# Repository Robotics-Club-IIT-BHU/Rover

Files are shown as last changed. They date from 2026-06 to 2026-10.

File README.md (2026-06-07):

# Rover
## Drive:
Clone the src file and build the package
then run using : ros2 launch drive sim.launch.py

## RtabMap:
Build RTABMAP ROS: https://github.com/introlab/rtabmap_ros
and run in second terminal using : ros2 launch rtabmap_launch rtabmap.launch.py    rgb_topic:=/camera/color/image_raw    depth_topic:=/camera/depth/image_raw    camera_info_topic:=/camera/camera_info    frame_id:=base_link    odom_topic:=/odom    approx_sync:=true

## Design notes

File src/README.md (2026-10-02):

# Athena

Athena is a six-wheeled outdoor rover (ROS 2 Humble, NVIDIA Jetson). Give it a
GPS coordinate, or click a point, and it drives there, steering around
obstacles it sees. A Pixhawk supplies IMU and GPS, a RealSense D435i supplies
obstacles and visual odometry, and a Raspberry Pi Pico drives the six motors.

This page is **how to run it**. How it is built: [docs/ARCHITECTURE.md](docs/ARCHITECTURE.md).

| I want to | Read |
|---|---|
| Understand the packages, data flow, frames, design decisions | [docs/ARCHITECTURE.md](docs/ARCHITECTURE.md) |
| Run, tune, test or fix navigation | [athena_gps_nav/README.md](athena_gps_nav/README.md) |
| Wire (pin map), calibrate, flash or debug the motors | [athena_drive/README.md](athena_drive/README.md) |
| SSH in, get through WiFi login, use `rviz2` from a laptop | [athena_remote/README.md](athena_remote/README.md) |
| Every Foxglove panel, goal, waypoint and troubleshooting step | [athena_remote/docs/FOXGLOVE_PANEL.md](athena_remote/docs/FOXGLOVE_PANEL.md) |
| Test navigation from the Foxglove panel | [athena_remote/TESTING.md](athena_remote/TESTING.md) |
| Change code, build, use git | [CONTRIBUTING.md](CONTRIBUTING.md) |

## Contents

1. [Get a shell on the rover](#1-get-a-shell-on-the-rover)
   - [Log in to the institute WiFi](#log-in-to-the-institute-wifi)
2. [Bring the rover up](#2-bring-the-rover-up)
3. [Check it is healthy](#3-check-it-is-healthy)
4. [Connect Foxglove (the control panel)](#4-connect-foxglove-the-control-panel)
5. [Send it somewhere](#5-send-it-somewhere)
6. [Everyday commands](#6-everyday-commands)
7. [Hardware](#7-hardware)
8. [Current state](#8-current-state-hardware-last-verified-september-2026)

---

## 1. Get a shell on the rover

Everything below is typed on the Jetson, over SSH:

```bash
ssh robo@172.20.119.87
```

`172.20.119.87` is the address on 2026-10-02. It changes with DHCP: on the
Jetson, `hostname -I` prints it; from another machine on the same WiFi,
`ssh robo@ubuntu.local` usually works. Finding it by scanning, and a host alias
that also opens the Foxglove tunnel:
[athena_remote](athena_remote/README.md#getting-a-shell-on-the-jetson).

`~/.bashrc` on the Jetson sources ROS and the workspace and sets
`ROS_DOMAIN_ID=42`. A shell that skips it (`ssh host 'command'`, cron) is on
domain 0 and sees an empty graph:
[fix](athena_remote/README.md#getting-a-shell-on-the-jetson).

### Log in to the institute WiFi

The institute WiFi puts a login page in front of the internet, and the Jetson has
no screen to show it on. Log it in from your SSH session instead. The login page
blocks only the internet, so you can still SSH to the Jetson from a laptop on the
same WiFi before it is logged in.

**1. Is a login needed?**

```bash
curl -s -o /dev/null -w "%{http_code}\n" http://connectivitycheck.gstatic.com/generate_204
```

`204` means it is already online and there is nothing to do. Anything else means
the login page is intercepting it.

**2. Log in by hand (first time, or when the automatic login fails).** `w3m` is a
text web browser, already installed on the Jetson:

```bash
w3m http://connectivitycheck.gstatic.com/generate_204
```

The login page opens in the terminal. Fill it in like a normal page:

| Key | Does |
|---|---|
| `Tab` / arrow keys | move between fields and buttons |
| `Enter` on a field | start typing; `Enter` again to accept |
| `Enter` on the login button | submit |
| `q`, then `y` | quit |

Run the `curl` from step 1 again: `204` means you are through.

**3. Let it log itself in (optional).** `captive_login` reads the login form once,
then logs in with your saved username and password:

```bash
ros2 run athena_remote captive_login --ros-args -p mode:=discover   # ONE TIME: writes ~/.config/athena_remote/portal.yaml
vim ~/.config/athena_remote/portal.yaml                             # fill in your username and password (i to type, Esc then :wq to save)
ros2 run athena_remote captive_login                                # log in (does nothing if already online)
```

Your password stays in `~/.config/athena_remote/portal.yaml` on the Jetson: it is
not in the repo, the file is readable only by you, and it is never logged.

**4. Stay logged in (optional).** Run `crontab -e` and add these two lines. The
first logs in at boot; the second re-logs in every 10 minutes if the session
expired:

```
@reboot      sleep 30 && . /opt/ros/humble/setup.sh && ~/athena/install/athena_remote/lib/athena_remote/captive_login
*/10 * * * * . /opt/ros/humble/setup.sh && ~/athena/install/athena_remote/lib/athena_remote/captive_login
```

Keep the `. /opt/ros/humble/setup.sh` part: without it the cron job fails
silently. Logged in but still no internet (`apt`, `git` fail): check
[the clock](#correcting-the-clock). If the automatic login fails (JavaScript login
pages, changing tokens):
[CAPTIVE_PORTAL.md](athena_remote/docs/CAPTIVE_PORTAL.md).

## 2. Bring the rover up

```bash
ros2 launch athena_gps_nav bringup.launch.py
```

One command starts the entire stack, staggered so each layer has what it
depends on before it starts. Give it about 40 seconds to settle.

| Elapsed | Starts | Why it waits |
|---|---|---|
| 0 s | RealSense camera, Pixhawk bridge, robot description | nothing works without sensor data |
| 0 s | Motor bridge | not delayed: it opens the Pico serial link, then waits for a `/cmd_vel` that only arrives once Nav2 is up |
| 5 s | Visual odometry (rtabmap) | needs camera images already flowing |
| 8 s | Both EKFs and the GPS transform | need odometry and IMU to fuse |
| 12 s | Nav2: planner, controller, costmaps | needs a position estimate before it can plan |
| 15 s | Foxglove bridge and the panel's nodes | only useful once there is data to show |

### Launch options

`bringup.launch.py` takes exactly these four arguments. Anything else is
silently accepted by `ros2 launch` and then ignored, so a typo costs you a run
(`--show-args` lists the real ones).

```bash
# motors receive no commands (logged, not sent); safe with the rover on a bench
ros2 launch athena_gps_nav bringup.launch.py dry_run:=true

# no RealSense: no obstacle avoidance AND no visual odometry, so the EKFs
# dead-reckon on the Pixhawk alone
ros2 launch athena_gps_nav bringup.launch.py use_camera:=false

# no control panel: lower CPU load
ros2 launch athena_gps_nav bringup.launch.py foxglove:=false

# indoor / no-GPS mode (explained below)
ros2 launch athena_gps_nav bringup.launch.py local_only:=true
```

**Indoors, use `local_only:=true`.** It drops `ekf_global` and `navsat_transform`
and publishes a static identity `map -> odom` instead. Nav2's configuration is
untouched (`global_frame` stays `map` everywhere), because with that transform
`map` *is* `odom`, so switching back to GPS work is just dropping the flag.

The reason is not CPU. With no GPS fix, `ekf_global` has nothing to fuse, so it
dead-reckons the same visual odometry and gyro that `ekf_local` already uses:
two independent filters on identical inputs, whose estimates slowly diverge for
no reason. That divergence *is* the `map -> odom` drift, and indoors it buys
nothing. Delete the second filter and the drift cannot happen
([more](docs/ARCHITECTURE.md#key-design-decisions)).

### Running one layer at a time

For debugging; `bringup.launch.py` is all of these together. Full list and
arguments: [athena_gps_nav](athena_gps_nav/README.md#run).

| Launch file | Starts |
|---|---|
| `athena_gps_nav sensors.launch.py` | robot description, camera, Pixhawk bridge, cloud downsampler |
| `athena_gps_nav vio.launch.py` | visual odometry and its gate |
| `athena_gps_nav localization.launch.py` | the EKFs and GPS transform |
| `athena_gps_nav navigation.launch.py` | Nav2 |
| `athena_drive drive.launch.py` | the motor bridge only |
| `athena_remote foxglove.launch.py` | the Foxglove bridge and panel nodes only |
| `athena_gps_nav bench_test.launch.py` | fake sensors and the real pipeline: no hardware at all |

## 3. Check it is healthy

```bash
ros2 run athena_gps_nav stack_check
```

It counts messages for a fixed window (10 s by default), prints one block per
stage, and exits on its own: there is nothing to Ctrl-C. For a longer sample:

```bash
ros2 run athena_gps_nav stack_check --ros-args -p window:=30.0
```

The full report also has a `TF TREE` section, a `NAV2` section, and a closing
`ALL CHECKS PASS` or `n FAIL` line. The part people read first, from a healthy
indoor run:

```
SENSORS
  [PASS]  pixhawk imu                 48.5 Hz
  [PASS]  imu physics (at rest)      |g|=9.81 m/s2, attitude-vs-accel residual 0.002, tilt r=+0 p=+0 deg
  [PASS]  pixhawk gps                  5.2 Hz, NO FIX (indoors?)
  [PASS]  depth cloud (camera)         6.6 Hz

OBSTACLE PERCEPTION  (depth camera -> costmap)
  [PASS]  downsampled cloud            6.6 Hz, 4812 pts/frame
  [PASS]  local costmap marking      767 lethal + 888 inflated cells
  [PASS]  global costmap marking     731 lethal + 902 inflated cells

ODOMETRY / LOCALIZATION
  [PASS]  VIO raw (rtabmap)           11.4 Hz
  [PASS]  VIO gated                   11.2 Hz (2 implausible dropped)
  [PASS]  EKF local (odom)            29.8 Hz
  [PASS]  EKF global (map)            27.3 Hz
  [FAIL]  navsat gps->map              0.0 Hz  (needs a GPS fix)
```

That single failure is expected without a GPS fix. Failures that are **not** faults:

- `navsat gps->map` FAILs whenever there is no fix.
- Launched with `local_only:=true`, `EKF global (map)` and `navsat gps->map` both
  FAIL, because neither node is started in that mode. That is the point of the mode.
- `NAV2 / cmd_vel` reads `0.0 Hz (idle - no goal sent)` and is never a FAIL. An
  idle `/cmd_vel` is the correct state with no goal running.

How to read the rest, and the hands-on tests:
[TESTING.md](athena_gps_nav/docs/TESTING.md#health-check).

## 4. Connect Foxglove (the control panel)

[Foxglove](https://foxglove.dev) is the rover's front end: a satellite map with
live GPS, the obstacle costmap in 3D, the camera feed, the planned path, and drive
controls in one window. It draws on your machine, so the Jetson keeps its CPU. You
need a browser (or the desktop app) and SSH access to the rover; nothing else.

- Web app (nothing to install): **[app.foxglove.dev](https://app.foxglove.dev)**
  (it will ask you to sign in)
- Desktop app: **[foxglove.dev/download](https://foxglove.dev/download)**, works
  identically
- Foxglove's own docs: [docs.foxglove.dev](https://docs.foxglove.dev)

```
Your machine                           Jetson
Foxglove --ws://localhost:8765-- ssh -L 8765 --> foxglove_bridge (127.0.0.1:8765)
```

**Use a current Foxglove.** The bridge speaks only the newer `foxglove.sdk.v1`
protocol; older builds are refused at the handshake with a bare HTTP 400 and no
message in the UI.

### Step 1: on the rover

`bringup.launch.py` already starts the bridge (the 15 s step above). Run this
yourself only when bringup is **not** running; a second copy gives duplicate nodes
and a bridge that cannot bind port 8765:

```bash
ros2 launch athena_remote foxglove.launch.py
```

It starts `foxglove_bridge` on port **8765**, bound to `127.0.0.1` only (nothing is
exposed to the network, which is why step 2 is not optional), plus six nodes the
panel depends on:

| Node | Used for |
|---|---|
| `goal_manager` | turning a typed or clicked lat/lon into a Nav2 goal |
| `waypoint_manager` | marking places and driving back to them |
| `trajectory` | the line showing where the rover has actually been |
| `teleop_mux` | manual driving with a speed limit you can change live |
| `panel_camera` | a small JPEG copy of the camera for the panel (5 Hz, about 30 KB a frame) |
| `panel_cloud` | a thinned copy of the depth cloud for the 3D view (2 Hz, about 1,500 points) |

The last two exist because the raw camera image (13.8 MB/s) and the costmap's
point cloud (0.9 MB/s) are far more than campus WiFi carries through the tunnel.
They do nothing while no panel is open, and the costmap and visual odometry still
use the full-quality data.

### Step 2: on your machine, open the tunnel

Leave this running in its own terminal:

```bash
ssh -N -L 8765:localhost:8765 robo@172.20.119.87      # or just: ssh athena  (alias, see section 1)
```

If it fails with `bind: Permission denied`, something else holds port 8765 on your
machine (common on Windows, where Hyper-V reserves port ranges). Use another local
port, and the same one in Foxglove:

```bash
ssh -N -L 18765:localhost:8765 robo@172.20.119.87     # then connect to ws://localhost:18765
```

### Step 3: connect

1. Open [app.foxglove.dev](https://app.foxglove.dev) (or the desktop app) and sign in.
2. **Open connection -> Foxglove WebSocket**.
3. URL: `ws://localhost:8765` -> **Open**.

Use `localhost`, not the Jetson's address: the web app is served over HTTPS, and
browsers block a plain `ws://` connection from an HTTPS page except to `localhost`.
`ws://172.20.119.87:8765` would be blocked even if it were reachable.

### Step 4: load the layout

The layout is the saved arrangement of panels, already pointed at the right
topics. Copy it from the rover (the import dialog reads from *your* machine):

```bash
scp robo@172.20.119.87:/home/robo/athena/src/athena_remote/config/athena_foxglove_layout.json .
```

Then in Foxglove: **Layout menu (top right) -> Import from file** ->
`athena_foxglove_layout.json`. That is the whole panel.

```
+-------------------------------+-----------------+-------------+
|                               |  SATELLITE MAP  |   CAMERA    |
|      3D VIEW                  |                 |             |
|                               +-----------------+-------------+
|                               |        |  CONTROLS  | READOUTS |
|                               | TELEOP |  (4 tabs)  | (8 tabs) |
+-------------------------------+--------+------------+----------+
```

| Panel | Shows |
|---|---|
| 3D | rover model, obstacle costmap, depth cloud, **orange** planned path, **cyan** driven trail, yellow waypoint pins |
| Satellite map | GPS position on satellite imagery, the trail, waypoint pins |
| Camera | the colour camera, as JPEG at 5 Hz |
| Teleop | arrow buttons to drive by hand |
| Controls | tabs *Mark*, *Return*, *Speed*, *Go to* |
| Readouts | tabs *Goal* (with the *Nav status* line: why the last goal ended), *Speed*, *Teleop*, *GPS fix*, *Saved places*, *Log*, *Goal pose*, *Nav feedback* |

What every marker in the 3D view means, and the Controls tabs one by one:
[FOXGLOVE_PANEL.md](athena_remote/docs/FOXGLOVE_PANEL.md#what-each-panel-shows).

### Adding or rebuilding panels by hand

If you would rather build a panel yourself, or one went missing, add it from
Foxglove's **Add panel** menu and give it these settings:

| Panel type | Settings |
|---|---|
| **3D** | Follow frame `odom`. Publish tool: pose topic `/athena/goal_click` (never `/goal_pose`). Topics on: `/local_costmap/costmap`, `/athena/points_preview` (thinned depth cloud), `/plan`, `/athena/trajectory`, `/athena/waypoints`, `/athena/goal_marker`, `/odometry/local`, `/local_costmap/published_footprint`. Rover model: panel settings -> **Custom layers -> Add URDF**, source **topic**, `/robot_description` |
| **Map** | Custom tile layer, URL `https://mt1.google.com/vt/lyrs=s&x={x}&y={y}&z={z}` (satellite), follow topic `/gps/fix`; also show `/athena/trajectory_geojson` and `/athena/waypoints_geojson` |
| **Image** | Image topic `/athena/camera/compressed`, calibration `/camera/camera/color/camera_info` |
| **Teleop** | Topic `/athena/teleop/cmd_vel`, publish rate 15; up = `linear-x` +1, down = `linear-x` -1, left = `angular-z` +1, right = `angular-z` -1 |
| **Publish** (one per button) | Topic and type, then the JSON value: `/athena/goal_text` `std_msgs/msg/String` `{"data": "25.2629548, 82.9838284"}` (Go to); `/athena/waypoint_save` and `/athena/waypoint_goto` `std_msgs/msg/String` (Mark, Return); `/athena/teleop/max_speed` `std_msgs/msg/Float32` `{"data": 0.35}` (Speed) |
| **Raw Messages** | Any topic, for readouts, e.g. `/gps/fix.status.status` for the fix state |
| **Log** | rosout, for the Log readout |

Panel names and menu wording shift a little between Foxglove versions; the topics
above are what matters.

### If it will not connect

| Symptom | Cause |
|---|---|
| Refused instantly, HTTP 400, nothing in the bridge log | Foxglove too old (see above). Update it |
| `ConnectionRefusedError` / nothing on 8765 | bridge not running: bringup has not reached 15 s, or it was launched with `foxglove:=false` |
| Connects, panels blank | wrong layout or topics: re-import the layout; check the topic names above |
| Map blank, model missing, camera blank, teleop does nothing, no path lines | [troubleshooting table](athena_remote/docs/FOXGLOVE_PANEL.md#troubleshooting) |
| Still laggy on a slow link | send less: lower the defaults of `camera_rate`, `camera_width` (e.g. 424) and `cloud_rate` in `athena_remote/launch/foxglove.launch.py`, then relaunch. Raw everything, on a fast wired LAN only: `topic_whitelist:="['.*']"` |
| Camera panel blank | the Image panel must use `/athena/camera/compressed`: re-import the layout (copy it over again first, it changed on 2026-10-02) |

Test the bridge itself from the Jetson, and the full table:
[FOXGLOVE_PANEL.md](athena_remote/docs/FOXGLOVE_PANEL.md#setup).

## 5. Send it somewhere

Three ways, once the panel is open:

- **Click in the 3D view.** Toolbar **Publish** tool, **Pose**; click the
  destination and drag to set heading. Works with or without a GPS fix: use this
  indoors. The layout publishes clicks on `/athena/goal_click`, where `goal_manager`
  converts them into the `map` frame once and sends the goal. Do **not** point the
  tool at `/goal_pose` directly: Foxglove stamps a click in the panel's display
  frame (`odom` or `base_link`), Nav2 Humble re-reads it at that stamp on every
  replan, and TF only keeps 10 s, so any goal not reached within about 10 s fails.
  Until 2026-10-02 that was the cause of nearly every "rejected" clicked goal.
- **Type a coordinate** in the *Go to* tab: `{ "data": "25.2629548, 82.9838284" }`.
  An optional third number is the final compass heading (0 = north, 90 = east);
  omit it and the rover finishes facing the way it travelled. Needs a GPS fix.
- **Drive by hand** with the teleop arrows. This cancels any running Nav2 goal,
  so autonomy and the operator never fight over the wheels.

**Why did a goal fail?** Read the *Nav status* line at the top of the *Goal*
readout tab (the same line appears in the bringup terminal from `nav_status`). It
names the reason, for example `FAILED ...: blocked: lethal costmap cells in the
rover's path and no detour found`, `goal is outside the planner's 100 x 100 m
window`, or `rover did not move 0.3 m in 30 s`, and says what to do. Every reason
it can give: [FOXGLOVE_PANEL.md](athena_remote/docs/FOXGLOVE_PANEL.md).

**Cancel a goal:** send `{ "data": "cancel" }` on the *Go to* topic, or nudge a
teleop arrow. The teleop STOP button does **not** cancel a goal.

**Mark a place and come back.** Drive there, open the *Mark* tab, name it; the
*Return* tab drives back. Waypoints are saved in
`~/.config/athena_remote/waypoints.yaml` on the Jetson and survive reboots.
GPS-tagged waypoints (a fix was available when saved) stay valid forever;
map-only ones last until the next restart, because the map origin moves when the
datum is re-locked.

**Record and follow a GPS route** from a terminal, no panel:
[athena_gps_nav](athena_gps_nav/README.md#send-it-somewhere). Not ready for
unattended use: absolute heading is not fused
([why](athena_gps_nav/docs/TUNING.md#heading-the-compass-is-not-used)).

The same actions as `ros2 topic pub`, and every topic:
[TOPICS.md](athena_remote/docs/TOPICS.md).

## 6. Everyday commands

| I want to | Do this |
|---|---|
| Start everything | `ros2 launch athena_gps_nav bringup.launch.py` (section 2) |
| Check it works | `ros2 run athena_gps_nav stack_check` (section 3) |
| Open the panel | `ssh -N -L 8765:localhost:8765 robo@172.20.119.87`, then Foxglove -> `ws://localhost:8765` (section 4) |
| Cancel a goal from a terminal | `ros2 topic pub --once /athena/goal_text std_msgs/String '{data: "cancel"}'` |
| See what the controller asks for | `ros2 topic echo /cmd_vel_nav` (`/cmd_vel` has six publishers) |
| Open RViz | `rviz2 -d ~/athena/src/athena_gps_nav/config/athena_bench.rviz`: [setup](athena_gps_nav/docs/TESTING.md#rviz) |
| Test or calibrate the motors | `ros2 run athena_drive calibrate` (a menu). **Stop the stack first** (the Pico's port is exclusive); wheels off the ground: [guide](athena_drive/README.md#calibration) |
| Check how the sensors are mounted | `python3 ~/athena/indoor_test/mount_check.py camera` (also `costmap`, `yaw`, `watch`): [guide](athena_gps_nav/docs/TESTING.md#camera-mount) |
| Find out why GPS has no fix | stop bringup, then `ros2 run athena_gps_nav gps_diagnose`: [guide](athena_gps_nav/docs/TROUBLESHOOTING.md#gps-has-no-fix) |
| Run ROS commands over SSH with no panel | [athena_remote, Option B](athena_remote/README.md#which-way-in) |
| Use a native `rviz2` / `ros2` on a laptop | [athena_remote, Option C](athena_remote/README.md#which-way-in) |
| Get the Jetson through campus WiFi login | `w3m http://connectivitycheck.gstatic.com/generate_204`, or [captive_login](athena_remote/docs/CAPTIVE_PORTAL.md) |

### Correcting the clock

A Jetson that boots offline starts with a wrong clock: TF lookups report
extrapolation into the future, and certificate validation fails, so `apt` and
`git` stop working.

```bash
timedatectl                                                          # want: System clock synchronized: yes
sudo systemctl restart systemd-timesyncd && sudo timedatectl set-ntp true     # once a network is available
```

With no network, set it by hand: `sudo timedatectl set-ntp false`, then
`sudo timedatectl set-time "YYYY-MM-DD HH:MM:SS"`, then `sudo timedatectl set-ntp true`.
Restart the stack after any manual clock change: nodes cache timestamps.

## 7. Hardware

| Device | Connection | Used by |
|---|---|---|
| RealSense D435i | USB 3 | camera driver |
| Pixhawk PX4 FMU v2 | USB serial, MAVLink **921600** baud (`/dev/serial/by-id/usb-3D_Robotics_PX4_FMU_v2.x_0-if00`) | `pixhawk_bridge` |
| Raspberry Pi Pico W | USB serial, 115200 baud (`/dev/serial/by-id/usb-Raspberry_Pi_Pico*`) | `motor_bridge`; firmware in [athena_drive](athena_drive/docs/FIRMWARE.md) |

- **Motor wiring and the Pico pin map** (which GPIO goes to which driver channel,
  with a wiring diagram): [athena_drive/README.md](athena_drive/README.md#pico-to-motor-driver-pin-map).
- Always address serial devices by `/dev/serial/by-id/...`. The `ttyACM*` numbers
  swap between boots, and the Pixhawk and the Pico have each held `ttyACM0`.
  **Never launch the old `drive` package**: it hardcodes `/dev/ttyACM1`, which can
  be the Pixhawk ([drive/README.md](drive/README.md)).
- The Pico's serial port has one owner. `motor_bridge`, `calibrate`, `wiring_check`
  and `calibrate_speed` all open it, and bringup already starts a bridge. Check
  with `fuser -v /dev/ttyACM*`.
- Prop the rover up (wheels off the ground) for every motor test, except
  `calibrate` stage 4 and `calibrate_speed -p mode:=topspeed`, which drive on the floor.

## 8. Current state (hardware last verified September 2026)

- **Working, verified on hardware:** IMU, camera, visual odometry, both EKFs,
  obstacle costmaps, Nav2 planning and execution of goals.
- **GPS has no satellite fix.** The module talks to the Pixhawk cleanly but reports
  zero satellites indoors and outdoors; the software path is ruled out and the
  antenna / RF path is suspected. `/gps/fix` still carries a lat/lon with
  `status: -1`, which is not a fix. Everything except GPS-referenced navigation
  works: use `local_only:=true` and click goals. Diagnosis:
  [TROUBLESHOOTING.md](athena_gps_nav/docs/TROUBLESHOOTING.md#gps-has-no-fix).
- **GPS waypoint following is not ready:** it also needs an absolute heading source
  (absolute yaw is not fused), see
  [TUNING.md](athena_gps_nav/docs/TUNING.md#heading-the-compass-is-not-used).
- **Motor calibration is half done.** `~/.config/athena_drive/params.yaml` holds
  `min_pwm: 20` and `track_width: 0.85` (measured), but not `max_wheel_speed` or
  `max_pwm`, so `motor_bridge` falls back to 0.7 m/s and 255 and logs
  `UNCALIBRATED ... max_wheel_speed, max_pwm` at startup. A `max_wheel_speed` of
  exactly `0.7` is the fallback, not a measurement. Run stage 4 on the floor before
  trusting a commanded distance:
  `ros2 run athena_drive calibrate --ros-args -p stages:=4`.
- **The Pico has not been reflashed with the `G` command**, so `calibrate` runs
  multi-motor tests one motor at a time
  ([FIRMWARE.md](athena_drive/docs/FIRMWARE.md#flashing)).
- **Recovery is deliberately reduced:** no Spin or BackUp, so a goal Nav2 cannot
  rescue fails cleanly and hands control back to the operator
  ([why](athena_gps_nav/docs/TUNING.md#recovery-behaviour)).

## Contributors

- **Jashan**: GPS navigation stack, drive package, remote access and control panel

Add your name here when you contribute. See [CONTRIBUTING.md](CONTRIBUTING.md).

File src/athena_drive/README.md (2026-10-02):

# athena_drive

Motor drive for the Athena rover: `/cmd_vel` -> Raspberry Pi Pico W -> 6 DC
motors, plus the tools to check the wiring and calibrate the speeds.

## Safety

- **Prop the rover up so the wheels spin free for every test**, except
  `calibrate` stage 4 and `calibrate_speed -p mode:=topspeed`, which drive on the
  floor to measure distance and say so before they move. A reversed motor found on
  the bench is a five-minute fix; found on the floor it is a chase.
- Two watchdogs: `motor_bridge` zeroes its command if `/cmd_vel` is stale for
  0.5 s, and the Pico firmware stops the motors if serial is quiet for 500 ms.
  Pulling the Pico's USB cable is the fastest stop you have.
- **The Pico's serial port is exclusive.** `motor_bridge`, `calibrate`,
  `wiring_check` and `calibrate_speed` all want it, and `bringup.launch.py` already
  starts a `motor_bridge`. The second one loses, quietly: `calibrate` exits with
  `could not open`; a second bridge logs `could not open ... - running dry` and
  streams to nothing. A port conflict is the commonest cause of "`/cmd_vel` does
  nothing". Stop the stack before using the calibration tools, and check who
  holds the port with:

```bash
fuser -v /dev/ttyACM*
```

## Quick start

```bash
# ONE TIME: guided, interactive, saves what it measures
ros2 run athena_drive calibrate

# motors only, no navigation
ros2 launch athena_drive drive.launch.py
ros2 run athena_drive teleop         # arrows drive; releasing them stops the rover
```

### What each command runs

| Command | What it runs | Opens the Pico's port? |
|---|---|---|
| `ros2 run athena_drive calibrate` | the interactive menu: motor tests, direction check, deadband, top speed, track width ([below](#calibration)) | yes |
| `ros2 launch athena_drive drive.launch.py` | one node, `motor_bridge`: turns `/cmd_vel` into `V <left> <right>` serial commands for the Pico | yes |
| `ros2 run athena_drive teleop` | a keyboard node that publishes `/cmd_vel` (arrows, `q/z` linear speed, `e/c` angular speed, space stop). Needs `motor_bridge` running to do anything | no |
| `ros2 run athena_drive wiring_check` | drives motors on a schedule, no questions asked ([modes](docs/CALIBRATION.md)) | yes |

Only one process can hold the Pico's port at a time (see Safety above).

For full navigation use `ros2 launch athena_gps_nav bringup.launch.py`, which
includes `drive.launch.py`: do not also run it yourself. A shell that skipped
`~/.bashrc` (`ssh host 'command'`, cron) also needs `ROS_DOMAIN_ID=42` and both
`setup.bash` files sourced ([why](../athena_remote/README.md#option-b-ros-cli-over-ssh)).

## Pico to motor driver pin map

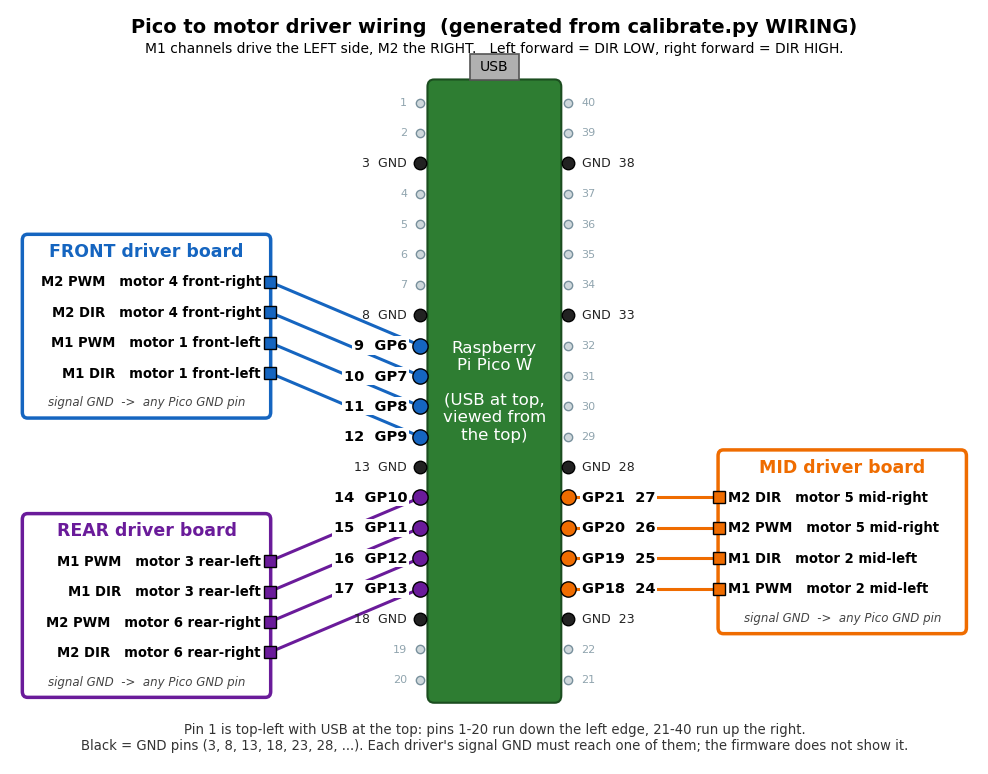
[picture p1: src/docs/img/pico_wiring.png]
Pico to motor driver wiring


GPIO number with the physical Pico header pin in brackets. Pin 1 is top-left
with USB at the top; pins 1-20 run down the left edge, 21-40 up the right.

| Motor | Driver channel | PWM | DIR |
|---|---|---|---|
| 1 front-left | FRONT M1 | GP8 (pin 11) | GP9 (pin 12) |
| 2 mid-left | MID M1 | GP18 (pin 24) | GP19 (pin 25) |
| 3 rear-left | REAR M1 | GP10 (pin 14) | GP11 (pin 15) |
| 4 front-right | FRONT M2 | GP6 (pin 9) | GP7 (pin 10) |
| 5 mid-right | MID M2 | GP20 (pin 26) | GP21 (pin 27) |
| 6 rear-right | REAR M2 | GP12 (pin 16) | GP13 (pin 17) |

- Left forward = DIR **LOW**, right forward = DIR **HIGH**.
- Each driver's signal GND must also go to a Pico GND pin (3, 8, 13, 18, 23, 28).
  This is not in the firmware.
- **Source of truth:** this table mirrors the `#define`s at the top of
  `firmware/athena_drive_fw/athena_drive_fw.ino` and the `WIRING` table in
  `athena_drive/calibrate.py`. If a wire moves to another GPIO, change **both**,
  reflash, and re-run `python3 ../docs/img/pico_wiring.py` to redraw the picture
  (it refuses to draw if the two files disagree).
- Board and channel names (FRONT/MID/REAR, M1/M2) are the firmware's
  `FRONT_M1` / `MID_M2` ... labels, not verified against the physical driver boards.
- `calibrate` menu `w` prints this map from the same table.

## Calibration

`ros2 run athena_drive calibrate` opens a menu (stop the stack first):

| Key | Does |
|---|---|
| `m` | **Manual motor test**: pick one or more motors, a direction, confirm; only that runs |
| `d` | direction check for the motors you pick |
| `w` | wiring map (the pin map above) |
| `s` | board status and invert flags, from the Pico |
| `1`-`5` | one stage: 1 directions, 2 side check, 3 PWM deadband, 4 top speed (**drives on the floor**), 5 track width |
| `a` | stages 1-5 in order |

Skip the menu with `-p stages:=m`, `-p stages:=3,4` or `-p stages:=all`.
Several motors run together through the firmware's `G <mask> <pwm>` command
(bit 0 = motor 1). `G` is compiled in the source but **not yet flashed to the
Pico**; until it is, `calibrate` runs the chosen motors one after another and
says so before you confirm.

Stage results, motor verdicts, what is saved where and manual tools:
[docs/CALIBRATION.md](docs/CALIBRATION.md).

**State today.** `~/.config/athena_drive/params.yaml` holds `min_pwm: 20` and
`track_width: 0.85` (both measured). `max_wheel_speed` and `max_pwm` are absent,
so the bridge runs on its estimates of 0.7 m/s and 255, and `motor_bridge` logs
an `UNCALIBRATED` warning naming them at startup. Run stage 4 on the floor
(`-p stages:=4`) before trusting a commanded distance.

## Nodes

Five executables, and there are no others:

| Node | Purpose |
|---|---|
| `motor_bridge` | `/cmd_vel` -> `V <l> <r>`; the one you run for navigation |
| `calibrate` | the menu and guided stages: directions, deadband, top speed, track width |
| `wiring_check` | drives one motor, a side, or a spin, to verify direction |
| `calibrate_speed` | measures `min_pwm` and `max_wheel_speed`, prints only |
| `teleop` | keyboard driving with a dead-man release |

All but `teleop` open the Pico's serial port. Launch file `drive.launch.py`
starts `motor_bridge`; `dry_run:=true` logs commands instead of sending them.

## Key parameters (motor_bridge)

Saved calibration is used unless a value is passed; passing one overrides it for
that run only (`ros2 launch athena_drive drive.launch.py max_pwm:=120`).

| Parameter | Estimate | Saved here today | Meaning |
|---|---|---|---|
| `track_width` | 0.40 | 0.85 | m between left and right wheel centres |
| `max_wheel_speed` | 0.7 | none | m/s at full PWM; scales every velocity Nav2 commands |
| `min_pwm` | 40 | 20 | static-friction deadband |
| `max_pwm` | 255 | none | cap; lower it for cautious testing |
| `max_accel` / `max_jerk` | 0.5 / 1.0 | | m/s^2, m/s^3: how hard and how smoothly it pulls away |
| `port` | `''` | | empty = auto-detect the Pico by USB id; never hard-code `/dev/ttyACM<n>` |

Full table, the firmware handshake, kinematics and the velocity profile:
[docs/MOTOR_BRIDGE.md](docs/MOTOR_BRIDGE.md).

## Docs

| Document | Covers |
|---|---|
| [docs/CALIBRATION.md](docs/CALIBRATION.md) | the `calibrate` menu and stages, where settings live, the single-purpose tools |
| [docs/FIRMWARE.md](docs/FIRMWARE.md) | serial commands, built-in safety behaviour, flashing the Pico |
| [docs/MOTOR_BRIDGE.md](docs/MOTOR_BRIDGE.md) | all parameters, serial port rules, kinematics, velocity profile, limitations |
| [docs/TESTING.md](docs/TESTING.md) | orientation checks, teleop -> Nav2 -> obstacles bring-up, first-drive order |
| [../docs/ARCHITECTURE.md](../docs/ARCHITECTURE.md) | where this package sits in the whole system |

## Contributors

- **Jashan**: firmware, motor bridge, velocity profile, calibration wizard

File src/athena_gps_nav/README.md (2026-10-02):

# athena_gps_nav

Outdoor navigation for the Athena rover: a depth camera to see obstacles, GPS
and an IMU to know where it is, and Nav2 to drive. ROS 2 Humble, Nav2 1.1.20,
robot_localization 3.5.4, rtabmap 0.23.7, Jetson.

This page is how to run it. How it works: [ARCHITECTURE.md](ARCHITECTURE.md).

| I want to | Read |
|---|---|
| Check the stack is healthy, test with RViz or by hand | [docs/TESTING.md](docs/TESTING.md) |
| Change a costmap, speed, GPS or filter parameter | [docs/TUNING.md](docs/TUNING.md) |
| Fix a sensor, GPS or camera problem; see known limitations | [docs/TROUBLESHOOTING.md](docs/TROUBLESHOOTING.md) |
| Understand the design and why it is the way it is | [ARCHITECTURE.md](ARCHITECTURE.md), [system overview](../docs/ARCHITECTURE.md) |

## Set up (once, per machine)

```bash
sudo apt install \
  ros-humble-nav2-bringup ros-humble-nav2-simple-commander \
  ros-humble-robot-localization ros-humble-rtabmap-odom \
  ros-humble-realsense2-camera ros-humble-imu-filter-madgwick \
  ros-humble-foxglove-bridge ros-humble-robot-state-publisher \
  ros-humble-xacro ros-humble-tf2-ros ros-humble-tf-transformations \
  ros-humble-sensor-msgs-py
pip3 install pymavlink

cd ~/athena                                  # the workspace root, never src/ or a package
colcon build --symlink-install
source install/setup.bash
ros2 run athena_drive calibrate              # motors, once; wheels off the ground
```

- `package.xml` does not declare `pymavlink` or `rtabmap_odom`; neither breaks the
  build, both surface as an `ImportError` or missing executable at launch.
- Build from `~/athena` with `--symlink-install` (traps explained in
  [CONTRIBUTING.md](../CONTRIBUTING.md)): `colcon` run from inside a package builds
  nothing and exits 0, and without the flag Python edits are ignored. With it,
  *editing* `config/`, `urdf/`, `launch/` or `behavior_trees/` takes effect on the
  next relaunch; *adding* a file needs a rebuild.
- Calibration is read by the motor bridge; until it exists the rover drives but not
  at the speeds Nav2 thinks it commanded ([athena_drive](../athena_drive/README.md)).
- **Do not** `source ~/rtab/install/setup.bash`: that source build is ABI-broken
  and crashes instantly. rtabmap comes from apt.
- `~/.bashrc` on this Jetson also sources `~/ros2_ws`, an unrelated rover project
  with its own from-source `realsense2_camera`. `sensors.launch.py` therefore
  starts the RealSense driver by absolute path to the apt binary; that is why its
  `executable=` looks odd.

## Run

```bash
ros2 launch athena_gps_nav bringup.launch.py          # everything; give it ~40 s
ros2 run athena_gps_nav stack_check                   # PASS/FAIL per stage, then exits
```

One command starts sensors, visual odometry, both filters, Nav2, the motor bridge
and the Foxglove panel, staggered so each layer has what it needs (order and
reasons: [system overview](../docs/ARCHITECTURE.md#launch-order)). These four are
the only arguments (`ros2 launch athena_gps_nav bringup.launch.py --show-args` is
authoritative; others are silently ignored):

| Argument | Effect |
|---|---|
| `dry_run:=true` | motor commands logged, not sent; safe on a desk |
| `use_camera:=false` | no RealSense: no obstacle avoidance **and** no visual odometry, so the local EKF has no translation source and `odom` will not track motion |
| `foxglove:=false` | no control panel, lower CPU |
| `local_only:=true` | indoor / no-GPS mode (below) |

**Indoors, use `local_only:=true`.** It drops `ekf_global` and `navsat_transform`
and publishes a static identity `map -> odom`; Nav2's config is untouched
(`global_frame` stays `map`) and switching back is dropping the flag. With no fix
`ekf_global` would dead-reckon the same inputs as `ekf_local`, and the two
diverging *is* the indoor `map -> odom` drift
([why](../docs/ARCHITECTURE.md#key-design-decisions)). `pixhawk_bridge` still
publishes `/gps/fix`. `stack_check` then reports `EKF global (map)` and `navsat
gps->map` as FAIL: expected.

Launch one layer at a time to debug it:

| Launch file | Arguments | Starts |
|---|---|---|
| `sensors.launch.py` | `use_camera` | robot description, camera driver, camera IMU filter, Pixhawk bridge, cloud downsampler |
| `vio.launch.py` | none | rtabmap visual odometry + `vio_gate` |
| `localization.launch.py` | `use_sim_time`, `local_only` | two EKFs + navsat_transform, or one EKF + static `map -> odom` |
| `navigation.launch.py` | `use_sim_time` | Nav2 |
| `bringup.launch.py` | `dry_run`, `use_camera`, `foxglove`, `local_only` | all of the above + motor bridge + Foxglove |
| `bench_test.launch.py` | none | fake sensors + the real pipeline; no hardware at all |

## Send it somewhere

- **Click:** RViz **2D Goal Pose** 2-3 m ahead in free space, or the Foxglove 3D
  panel. A path appears on `/plan` and `/cmd_vel` starts (`ros2 topic hz /cmd_vel`).
  With `dry_run:=true` nothing moves; `/cmd_vel` existing proves planning and control.
- **By GPS (needs a fix):** type a coordinate in the Foxglove *Go to* tab
  ([athena_remote](../athena_remote/docs/FOXGLOVE_PANEL.md#driving-it)), or record
  and replay a route (ENTER saves a waypoint; file format in
  `config/waypoints_example.yaml`):

```bash
ros2 run athena_gps_nav gps_waypoint_logger --ros-args -p output_file:=/home/robo/route.yaml
ros2 run athena_gps_nav gps_waypoint_follower --ros-args -p waypoints_file:=/home/robo/route.yaml
ros2 run athena_gps_nav gps_waypoint_follower --ros-args -p goal_lat:=25.26295 -p goal_lon:=82.98383   # one point
```

  Humble's Nav2 has no GPS waypoint action, so the follower converts each lat/lon
  through robot_localization's `/fromLL` and uses the ordinary waypoint follower.
  Absolute yaw is not fused, so map-frame bearings are dead-reckoned: read
  [TUNING.md](docs/TUNING.md#heading-the-compass-is-not-used) before trusting a
  recorded route.
- **A failed goal** (Nav2 here runs its own tree with no Spin or BackUp): clear
  costmaps, wait 5 s, up to 6 rounds, then fail cleanly and hand control back to
  you ([why](docs/TUNING.md#recovery-behaviour)).

## Nodes

The complete list of `ros2 run athena_gps_nav <exe>` targets:

| Node | Job |
|---|---|
| `pixhawk_bridge` | Pixhawk over MAVLink -> `/imu/data` and `/gps/fix`; aviation axes to ROS axes; HDOP to a real covariance |
| `vio_gate` | between visual odometry and the filters: drops motion the rover cannot have made, forces zero when parked |
| `pointcloud_downsampler` | thins the depth cloud so the costmaps are cheap to update |
| `stack_check` | one-shot PASS/FAIL health check |
| `localization_monitor` | records N seconds and writes an accuracy report |
| `costmap_drift_check` | measures whether the costmap slides when it should not |
| `gps_diagnose` | talks to the Pixhawk directly to explain why GPS has no fix. `argparse`, not a ROS node: `--seconds`, not `-p seconds:=` |
| `tf_check` | checks transforms are correctly *oriented*, not just present |
| `gps_waypoint_logger` / `gps_waypoint_follower` | record a route by driving it, then drive it autonomously |
| `fake_gps_imu` | synthetic GPS/IMU/VIO for `bench_test.launch.py`; not used on hardware |

Not in this package: motor control (`athena_drive`) and anything an operator
clicks (`athena_remote`).

## Key parameters

Tuning rationale and the rest: [docs/TUNING.md](docs/TUNING.md).

| Where | Parameter | Value |
|---|---|---|
| `nav2_params.yaml` | `desired_linear_vel` | 0.35 m/s |
| | `lookahead_dist` (fixed; `use_velocity_scaled_lookahead_dist: false`) | 1.0 m |
| | `rotate_to_heading_angular_vel` | 0.4 rad/s |
| | `xy_goal_tolerance` / `yaw_goal_tolerance` | 0.5 m / 3.14 rad |
| | local / global costmap | 8 x 8 m @ 0.05 m (`odom`) / 100 x 100 m @ 0.1 m (`map`) |
| | `inflation_radius` local / global | 0.9 / 1.2 m |
| | `obstacle_max_range` / `min_obstacle_height` / `expected_update_rate` | 3.0 m / 0.10 m / 2.0 s |
| | footprint | 1.3 x 1.0 m rectangle |
| `dual_ekf_navsat.yaml` | `navsat_transform: delay` | 45 s (pin a datum for repeatable runs) |
| | absolute yaw (`imu0_config` index 5) | false in both EKFs; gyro rate only |
| `pixhawk_bridge` | `baud`, `imu_rate_hz`, `gps_uere`, `gps_sigma_floor` | 921600, 50, 1.74, 3.06 |

Other files: `behavior_trees/athena_nav_to_pose.xml` (the tree), `urdf/athena.urdf.xacro`
(sensor positions; the camera offsets are load-bearing, re-measure with
`mount_check.py` after any remount, see [TESTING.md](docs/TESTING.md#camera-mount)),
`config/athena_bench.rviz`, `config/waypoints_example.yaml`.

## Contributors

- **Jashan**: the whole stack: sensor bridges, dual-EKF tuning, VIO gating, costmap work

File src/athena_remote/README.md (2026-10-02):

# athena_remote

The operator's side of the rover. Two jobs:

1. **Control panel.** A Foxglove front end to watch and drive the rover, plus
   the nodes behind it: GPS goals, saved waypoints, travelled trail,
   speed-limited teleop.
2. **Getting to the rover at all.** Shell access, WiFi captive-portal login,
   and viewing the ROS graph from a laptop on a network that blocks DDS.

Nothing here is needed for the rover to navigate. Kill all of `athena_remote`
and it still drives a route; it just has no convenient way to be told where to go.

## Everyday commands

```bash
# Jetson: already running if you used bringup.launch.py. Do not run it twice.
ros2 launch athena_remote foxglove.launch.py

# your machine: open and leave running, then connect Foxglove to ws://localhost:8765
ssh -N -L 8765:localhost:8765 robo@172.20.119.87

# any ROS command on the Jetson, no Foxglove (the export is not optional, see Option B)
ssh robo@172.20.119.87 'export ROS_DOMAIN_ID=42; source ~/athena/install/setup.bash && ros2 topic hz /odometry/local'
```

Panel walkthrough, goals, waypoints and troubleshooting:
[docs/FOXGLOVE_PANEL.md](docs/FOXGLOVE_PANEL.md).

### What actually runs

| Process | Started by | Job |
|---|---|---|
| `foxglove_bridge` | `foxglove.launch.py` (and `bringup.launch.py`) | serves ROS topics to Foxglove over one WebSocket, port 8765, loopback only |
| `goal_manager` | `foxglove.launch.py` | typed or clicked lat/lon -> Nav2 goal; understands `cancel` |
| `waypoint_manager` | `foxglove.launch.py` | save a named place, drive back to it |
| `trajectory` | `foxglove.launch.py` | publishes the driven path as the trail |
| `teleop_mux` | `foxglove.launch.py` | panel arrows -> `/cmd_vel`, cancelling any running goal first |
| `panel_camera` | `foxglove.launch.py` | colour camera -> throttled JPEG on `/athena/camera/compressed`; idle while nobody watches |
| `panel_cloud` | `foxglove.launch.py` | depth cloud -> voxel-thinned copy on `/athena/points_preview` for the 3D view; idle while nobody watches |
| `captive_login` | by hand: `ros2 run athena_remote captive_login` | logs the Jetson into a WiFi captive portal |

The first five run on the Jetson; none of them is needed for the rover to
navigate. `ssh` and the tunnel run on your own machine.

## Which way in

All three are verified working.

| You want | Use |
|---|---|
| Drive the rover, watch costmap, GPS, camera | **Option A, Foxglove panel.** Needs only a browser and SSH. Start here. See [docs/FOXGLOVE_PANEL.md](docs/FOXGLOVE_PANEL.md) |
| Run a command, check a rate, launch something | **Option B, ROS CLI over SSH.** Below |
| `rviz2` and native `ros2` tools on your laptop | **Option C, CycloneDDS.** Below. Worth the setup only for native tooling |

Why ROS 2 does not just work across managed WiFi: see the start of Option C.
SSH works because it is one outbound TCP connection, which such networks always
allow; every option here makes ROS look like that.

## Foxglove launch arguments

`foxglove.launch.py` declares sixteen arguments, and these are all of them. Add
`operator_nodes:=false` for the bridge alone.

| Argument | Default | Does |
|---|---|---|
| `port` | 8765 | bridge TCP port |
| `address` | 127.0.0.1 | loopback only; `0.0.0.0` listens on the network, and the bridge has no authentication |
| `topic_whitelist` | light set | regex list of served topics; `"['.*']"` for everything, including the 13.8 MB/s raw image (wired LAN only) |
| `operator_nodes` | true | the five panel nodes |
| `trajectory_source` | `/odometry/global` | use `/odometry/local` with no GPS fix; `bringup.launch.py` sets it from `local_only` |
| `max_speed` | 0.35 | m/s at full teleop stick |
| `max_turn` | 0.8 | rad/s at full teleop stick |
| `num_threads` | 3 | bridge worker threads |
| `max_qos_depth` | 2 | per-topic queue before the bridge sends |
| `message_backlog_size` | 200 | one shared outbox across every channel |
| `camera_rate` | 5.0 | panel camera JPEG frames per second |
| `camera_quality` | 70 | panel camera JPEG quality, 1-100 |
| `camera_width` | 0 | panel camera width in px, 0 = native 640 |
| `cloud_rate` | 2.0 | panel point cloud messages per second |
| `cloud_voxel` | 0.10 | panel point cloud: keep one point per cube of this size, m |
| `cloud_max_points` | 2000 | panel point cloud: cap per message |

## Getting a shell on the Jetson

```bash
ssh robo@172.20.119.87
```

`172.20.119.87` is the address on 2026-10-02 (it was `172.20.58.70` before). It
changes with DHCP: see "The address changes with DHCP" below to find it.

If you will do this often, add a host alias on your own machine. `ssh athena`
then also opens the Foxglove tunnel:

```
Host athena
    HostName 172.20.119.87
    User robo
    ForwardAgent yes
    LocalForward 8765 localhost:8765
```

`ForwardAgent` lets `git push` from the Jetson sign as you rather than as the
shared `robo` account; setup is in
[CONTRIBUTING.md section 6](../CONTRIBUTING.md#6-working-on-the-jetson-with-your-own-github-account).
No password for the account is recorded in this repository: ask a teammate for access.

**The address changes with DHCP.** From a machine already on the network:

```bash
ssh robo@ubuntu.local                      # mDNS: the Jetson's hostname is `ubuntu`, avahi is running
sudo nmap -sn 172.20.119.0/24 | grep -B2 -i nvidia   # or scan; widen to 172.20.0.0/17 if it moved far
```

Look for an NVIDIA vendor string, not Raspberry Pi (the Pico is behind USB, not
on the network). `nmap` is not installed on the Jetson or on most laptops
(`sudo apt install nmap`), and needs `sudo` to print MAC vendors. Without it,
ping-sweep and read the ARP table:

```bash
for i in $(seq 1 254); do ping -c1 -W1 172.20.119.$i >/dev/null & done; wait; ip neigh | grep -i REACHABLE
```

On the Jetson itself: `hostname -I`, or `ip -4 -o addr show scope global | awk '{print $2, $4}'`.
Ask the network admin for a DHCP reservation on the Jetson's MAC so the
address (and the tunnel command) stops changing.

**ROS environment.** `~/.bashrc` on the Jetson sources ROS and the workspace
and sets `ROS_DOMAIN_ID=42`. A shell that skips it (for example
`ssh host 'some command'`, which is non-interactive) lands on domain 0 and sees
nothing. If a shell reports no topics:

```bash
export ROS_DOMAIN_ID=42
source /opt/ros/humble/setup.bash
source ~/athena/install/setup.bash
```

## WiFi captive portal

Campus WiFi intercepts the Jetson with a login page it has no screen to show.
From the SSH session:

```bash
w3m http://connectivitycheck.gstatic.com/generate_204   # a text browser; 204 = through, a page = portal
ros2 run athena_remote captive_login --ros-args -p mode:=detect     # is a portal in the way?
ros2 run athena_remote captive_login --ros-args -p mode:=discover   # ONE TIME: write ~/.config/athena_remote/portal.yaml
ros2 run athena_remote captive_login                                # log in (after filling in portal.yaml)
```

Details, JavaScript portals and the cron re-login:
[docs/CAPTIVE_PORTAL.md](docs/CAPTIVE_PORTAL.md). Still offline after
logging in: check the clock ([root README](../README.md#correcting-the-clock)).

## Option B: ROS CLI over SSH

The simplest thing that works, with one required export:

```bash
ssh robo@172.20.119.87 'export ROS_DOMAIN_ID=42; source ~/athena/install/setup.bash && ros2 topic list'
ssh robo@172.20.119.87 'export ROS_DOMAIN_ID=42; source ~/athena/install/setup.bash && ros2 run athena_gps_nav stack_check'
```

`ssh host 'command'` runs a non-interactive shell, and `~/.bashrc` starts with
the stock Ubuntu guard (`case $- in *i*) ;; *) return;; esac`), so it returns
before reaching `export ROS_DOMAIN_ID=42`. The command then runs on domain 0
while every node is on 42, and you get an empty graph that looks like a
network fault or a stack that is not running. Sourcing `install/setup.bash`
does not help (it sets package paths, not the domain). Diagnose with:

```bash
ssh robo@172.20.119.87 'echo "domain=[$ROS_DOMAIN_ID] rmw=[$RMW_IMPLEMENTATION]"'
# domain=[] rmw=[]   <- the failure, not a network problem
```

A shell function on your laptop makes it feel local:

```bash
jros() { ssh robo@172.20.119.87 "export ROS_DOMAIN_ID=42; source ~/athena/install/setup.bash && ros2 $*"; }
# then:  jros topic list      jros topic echo /gps/fix
```

If the stack was started from a shell that had `athena_env.sh` sourced (Option
C), also `export RMW_IMPLEMENTATION=rmw_cyclonedds_cpp` in the command: the CLI
must use the same middleware as the nodes it inspects.

## Option C: native ROS on a laptop

The CycloneDDS setup guide. For `rviz2` and `ros2 topic echo` running on your own machine against the
Jetson's live graph. Driving the rover and watching costmap, GPS and camera
needs only Foxglove, which is simpler.

**Why it is needed.** ROS 2 has no master. Nodes find each other by DDS
discovery: a multicast announcement to `239.255.0.1`, direct replies, then data
over a wide range of UDP ports. Managed WiFi breaks each step: it drops
multicast, **AP/client isolation** stops clients reaching each other, and it
firewalls the UDP range. `ROS_DOMAIN_ID` only partitions traffic on a network
that already carries it; it does not help machines find each other. Three
problems must be solved, in order:

1. **IP reachability** between the two machines.
2. **Discovery without multicast**: CycloneDDS with an explicit unicast peer.
3. **The same middleware on both machines.** Two ROS 2 machines on different
   RMWs never discover each other, whatever the domain and peers. Nothing
   reports it: both sides come up clean and see nothing.

**Prerequisite.** The laptop runs ROS 2 Humble on Ubuntu 22.04 and every shell
has `source /opt/ros/humble/setup.bash`. Install `ros-humble-desktop` for
`rviz2` (or at least `ros-humble-rviz2`), or `ros-humble-ros-base` if
`ros2 topic echo` is enough. No version
mixing: Cyclone on Humble will not talk to a Jazzy or Foxy machine.

### Step 1: IP reachability

```bash
ping <jetson-ip>        # from the laptop, e.g. 172.20.119.87
```

If it works, go to step 2. If not, the network isolates clients and you need an
overlay VPN, on **both** machines:

```bash
curl -fsSL https://tailscale.com/install.sh | sh
sudo tailscale up
tailscale ip -4                                     # note each 100.x.y.z
```

`ping 100.x.y.z` (the other machine) must work before continuing.

### Step 2: install CycloneDDS on the laptop

Already installed on the Jetson, alongside FastDDS.

```bash
sudo apt install ros-humble-rmw-cyclonedds-cpp
```

### Step 3: copy the helper to the laptop

`athena_env.sh` finds `cyclonedds_peers.xml` at `../config/` relative to itself,
so keep the sibling `scripts/` and `config/` layout. Copy only the `.sh` and it
fails with `cyclonedds_peers.xml not found` (its fallback, `ros2 pkg prefix
athena_remote`, only helps on a machine with this workspace built, which the
laptop is not):

```bash
mkdir -p ~/athena_net/scripts ~/athena_net/config
scp robo@172.20.119.87:/home/robo/athena/src/athena_remote/scripts/athena_env.sh ~/athena_net/scripts/
scp robo@172.20.119.87:/home/robo/athena/src/athena_remote/config/cyclonedds_peers.xml ~/athena_net/config/
```

### Step 4: source it on both machines, pointed at the other one

```bash
# laptop  -> the Jetson's address
source ~/athena_net/scripts/athena_env.sh 172.20.119.87

# Jetson  -> the laptop's address
source ~/athena/src/athena_remote/scripts/athena_env.sh <laptop-ip>
```

**Source it on the Jetson BEFORE launching the stack.** `RMW_IMPLEMENTATION` is
not set in the Jetson's `~/.bashrc`, so a normal shell there runs the default
`rmw_fastrtps_cpp`. A stack launched from such a shell never discovers a
Cyclone laptop, with no error on either side, and running nodes cannot be
switched: restart them under the new environment.

The script is equivalent to these, where the `CYCLONEDDS_URI` path is wherever
you put the XML on *that* machine (`ATHENA_PEER` is substituted into the XML's
`<Peer address="${ATHENA_PEER}"/>`, so the file needs no editing):

```bash
export RMW_IMPLEMENTATION=rmw_cyclonedds_cpp
export ATHENA_PEER=<the other machine's address>
export CYCLONEDDS_URI=file://$HOME/athena_net/config/cyclonedds_peers.xml
export ROS_DOMAIN_ID=42      # the script defaults to 42 and leaves an existing value alone
ros2 daemon stop             # the daemon caches the old (multicast) middleware config
```

**No files at all.** `CYCLONEDDS_URI` also accepts literal XML, so one export
replaces the script and config on the laptop:

```bash
export RMW_IMPLEMENTATION=rmw_cyclonedds_cpp && export ROS_DOMAIN_ID=42 && export CYCLONEDDS_URI='<CycloneDDS><Domain id="any"><General><Interfaces><NetworkInterface autodetermine="true" priority="default" multicast="false"/></Interfaces><AllowMulticast>false</AllowMulticast></General><Discovery><Peers><Peer address="172.20.119.87"/></Peers></Discovery></Domain></CycloneDDS>' && ros2 daemon stop
```

Cyclone picks a network interface itself. If a machine has several (`docker0`, a
VPN, WiFi) and it picks wrong, name one in `config/cyclonedds_peers.xml`:
`<NetworkInterface name="tailscale0" priority="default" multicast="false"/>`.

**`ROS_DOMAIN_ID` must match on both sides: the rover is on 42.** The script
keeps a value that is already set, so an inherited wrong one survives it.
Check, and if a shell disagrees, set it and restart the daemon (which caches the
domain too):

```bash
echo $ROS_DOMAIN_ID
export ROS_DOMAIN_ID=42 && ros2 daemon stop
```

### Step 5: verify, from the laptop

```bash
ros2 topic list
ros2 topic echo /odometry/local
```

RViz: `athena_bench.rviz` is in this workspace on the Jetson, not on the laptop.
Copy it, then open it (plain `rviz2` also works; add the displays by hand, see
[athena_gps_nav RViz setup](../athena_gps_nav/docs/TESTING.md#rviz)):

```bash
scp robo@172.20.119.87:/home/robo/athena/src/athena_gps_nav/config/athena_bench.rviz ~/athena_net/
rviz2 -d ~/athena_net/athena_bench.rviz
```

Verified on this rover: with `AllowMulticast=false` and a single unicast peer,
topic discovery and data transfer both work, and the `${ATHENA_PEER}`
substitution in the XML works.

### If it does not work

Test the simplest pair before touching RViz:

```bash
ros2 run demo_nodes_cpp talker      # Jetson
ros2 run demo_nodes_cpp listener    # laptop
```

`demo_nodes_cpp` is on the Jetson and comes with `ros-humble-desktop`; a
`ros-humble-ros-base` laptop needs `ros-humble-demo-nodes-cpp`. If that fails,
so will everything else:

| Symptom | Cause |
|---|---|
| `ros2 topic list` shows only `/rosout`, `/parameter_events` | wrong peer address, a stale daemon (`ros2 daemon stop`), or different RMWs: `echo $RMW_IMPLEMENTATION` on both, including in the shell the stack was launched from |
| nothing at all, and `ping` fails | step 1: no IP route between the machines |
| topics listed but `echo` hangs | discovery works, data does not: usually a firewall on the laptop |
| works, then stops after a reboot | the env vars are per-shell; add the `source` line to `~/.bashrc` |

### Notes

- **FastDDS** (the default RMW) can do this too, through a Discovery Server or
  TCP transport, but neither worked reliably here: with TCP the sockets
  connected and RTPS logical-port negotiation failed (*"Cannot find an
  available logical port"*). CycloneDDS with an explicit peer is simpler and is
  what was verified.
- **The Jetson's actual desktop.** `gnome-remote-desktop` is running: VNC on
  5900, RDP on 3389. Prefer RDP (much faster on GNOME 42 under Wayland):
  `ssh -N -L 3389:localhost:3389 robo@172.20.119.87`, then RDP to `localhost`.
  It costs the Jetson a full CPU core, dropping visual odometry from ~11 Hz to
  ~5 Hz: fine for a look, not for measurements.

## Docs

| Document | Covers |
|---|---|
| [docs/FOXGLOVE_PANEL.md](docs/FOXGLOVE_PANEL.md) | panel setup, what each panel shows, goals, teleop, waypoints, bandwidth, panel troubleshooting |
| [docs/TOPICS.md](docs/TOPICS.md) | every topic the panel nodes publish or subscribe to, plus `ros2 topic pub` equivalents |
| [docs/CAPTIVE_PORTAL.md](docs/CAPTIVE_PORTAL.md) | WiFi portal login: `w3m`, `captive_login`, cron |
| [TESTING.md](TESTING.md) | testing navigation from the panel and telling why it did what it did |

## Contributors

- **Jashan**: control panel, goal and waypoint nodes, remote access, captive-portal login

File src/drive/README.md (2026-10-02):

# drive (deprecated)

**Do not use this package. Use [`athena_drive`](../athena_drive/README.md).**

`move.py` defaults `port` to a **hardcoded `/dev/ttyACM1`**. On this rover the
Pico and the Pixhawk swap `ttyACM` numbers between boots, and the autopilot lands
on `ttyACM1` about half the time, so this package can send PWM commands to a flight
controller. `athena_drive/motor_bridge` globs
`/dev/serial/by-id/usb-Raspberry_Pi_Pico*`, which is stable per board.
Nothing in the current stack runs this package: `bringup.launch.py` includes
`athena_drive/launch/drive.launch.py`. It remains only so older branches still build.

`athena_drive` also has what this lacks: the calibration wizard (this package's
parameters are not persisted), the jerk-limited velocity profile, the firmware
handshake and per-motor wiring checks.

If you must run it, pass the port explicitly and stop anything else holding the
Pico's serial port (including bringup's `motor_bridge`):

```bash
ros2 run drive move --ros-args -p port:=$(readlink -f /dev/serial/by-id/usb-Raspberry_Pi_Pico*)
ros2 run drive move --ros-args -p dry_run:=true            # log instead of driving
ros2 run drive move --ros-args -p legacy_protocol:=true    # Pico on the pre-v2 sketch (F/B/L/R/S)
ros2 run drive teleop                                      # arrows, q/z linear speed, e/c angular speed, space stop; releasing stops
```

Firmware here is `firmware/sketch_feb10a/`; flash `athena_drive/firmware/athena_drive_fw/`
instead (`~/Desktop/sketch_feb10a` is an older, diverged copy). `move` parameters
(`max_wheel_speed` 0.7, `track_width` 0.40, `min_pwm` 40, `invert_left`/`invert_right`)
have the same meanings as in `athena_drive`'s [`motor_bridge`](../athena_drive/docs/MOTOR_BRIDGE.md#parameters),
but there is no `max_pwm` here.

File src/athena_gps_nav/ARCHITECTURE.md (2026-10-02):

# How Athena navigates

This explains *how* the navigation stack works. If you just want to run it,
read [README.md](README.md) instead.

Read this after you have seen the stack running once. It will make far more
sense with the picture in front of you.

**Contents**

- [The big picture](#the-big-picture). The two questions the rover answers
- [What is around me?](#chain-1-what-is-around-me). Camera to obstacle map
- [Where the camera is bolted](#where-the-camera-is-bolted-and-why-it-decides-everything). The geometry the costmap believes
- [Where am I?](#chain-2-where-am-i). Three sensors into one position
- [Indoors: one filter, not two](#indoors-one-filter-not-two). What `local_only` changes and why
- [How it decides to move](#how-it-decides-to-move). Planner, controller, and the lookahead trap
- [Recovery](#recovery-why-spin-and-backup-were-removed). Why the stock tree was wrong for this rover
- [Every file in this package](#every-file-in-this-package). What each script does
- [What we did differently](#what-this-differs-from-and-why), and why the reference code did not work
- [Verified results](#verified-results). Measured numbers, not claims

---

# How it all works

Read this once you have seen the stack running. It will make more sense.

## The big picture

Everything the rover does comes down to answering two questions, then
acting on them:

```mermaid
flowchart LR
    S["SENSORS<br/>camera, GPS, IMU"] --> A["Where am I?"]
    S --> B["What is around me?"]
    A --> N["NAV2<br/>plan and steer"]
    B --> N
    N --> M["MOTORS"]
```

Those two questions are answered by two completely separate chains that
only meet inside Nav2. That separation is deliberate: if GPS drops out, the
"what is around me" chain is untouched and the rover keeps avoiding
obstacles.

## Chain 1. What is around me?

The depth camera is the only obstacle sensor. There is no lidar.

```mermaid
flowchart LR
    CAM["D435i camera<br/>640x480 depth @ 15 fps<br/>decimated 2x in the driver"] --> PTS["3D point cloud<br/>up to ~77k points, 7.0 Hz"]
    PTS --> DS["downsampler<br/>keep 1 in 8,<br/>keep 0.25 to 3.5 m"]
    DS --> CM["costmap<br/>mark cells with points<br/>clear what the camera sees empty"]
    CM --> INF["inflation<br/>add safety halo"]
    INF --> NAV["Nav2 plans<br/>around it"]
```

Step by step:

1. **The camera produces a 3D point cloud**. Building that cloud is the
   most expensive stage on the Jetson, so the driver decimates the depth
   image 2x *before* the pointcloud block: 640x480 becomes 320x240, so at
   most ~77,000 points rather than the ~307,000 a full-resolution frame
   would give, and fewer again once invalid depth pixels drop out. Obstacle
   marking at 5 cm costmap resolution does not need the extra detail. Depth and colour both run at 15 fps because VO only needs
   ~10 Hz and 30 fps starves the CPU. Measured arrival rate: 7.0 Hz.
2. **The downsampler thins it.** It keeps roughly one point in eight
   (`scarcity: 8`) and discards anything past 3.5 m or closer than 0.25 m,
   the latter being self-hits on the rover's own structure. About 4,300
   points survive at 7.4 Hz, which is plenty.
3. **The costmap turns points into a grid.** Every cell containing points
   becomes an obstacle. Crucially it also does the reverse: any cell the
   camera can see *through* is erased. That is why obstacles disappear
   when you move them away.
4. **The inflation layer adds a safety halo** so Nav2 plans around
   obstacles with clearance rather than grazing them.

There are two of these maps: a small fast one near the rover for steering,
and a big slow one for planning longer routes.

| | local | global |
|---|---|---|
| frame | `odom` | `map` |
| size, resolution | 8 x 8 m @ 0.05 m | 100 x 100 m @ 0.1 m |
| inflation radius / scaling | 0.9 m / 3.0 | 1.2 m / 2.0 |
| `always_send_full_costmap` | True | False |

Both are rolling windows, because there is no prior map: the costmap
follows the rover rather than covering a fixed area. A rolling window can
only see width/2 in any direction, which is why the global one is 100 m and
not 60: at 60 m every planned leg was capped at about 30 m.

The two differences between them are the interesting part. The **global**
map shapes the route, so it inflates wider and more gently, and the planner
curves away from obstacles early rather than reacting once they are close.
The **local** map controls, so it stays tight with a steeper factor;
inflating it as wide as the global one would box the controller in and it
would start refusing gaps the rover actually fits through. Both radii must
stay at or above the footprint's circumscribed radius, `hypot(0.65, 0.5)` =
0.82 m, or there is no cost gradient covering the rover's own corner sweep.

`always_send_full_costmap` diverges for a plainer reason: at 100 x 100 m
and 0.1 m the global grid is 1e6 cells, and republishing all of them at
1 Hz is roughly 1 MB/s down an SSH tunnel. The local grid is 160 x 160
cells and costs nothing to send whole.

### Obstacles: what clears them

Both costmaps used `nav2_costmap_2d::VoxelLayer`. It clears a voxel only
when a ray from the camera passes through it to a return *behind* it, and
nothing decays. Its observation source height-filters the cloud before using
it for marking *or* clearing, so with `min_obstacle_height: 0.10` the floor,
about 60% of the cloud, never cast a single ray (on the live stack every
clearing endpoint was at z >= 0.115). The rays that were left, from a lens
0.65 m up to things at least 0.20 m tall, pass above the lower part of
anything that has since been removed. A box taken away from 1.5 m in front
of the rover stayed 100% marked, both in a harness and in a replay of the
real camera. A floor-only clearing source only partly fixes this: it clears
low objects close in, but a voxel with open sky or nothing within 3.5 m
behind it can never be cleared by a ray. On the real recording it still
left 72% of the box.

Both costmaps now use spatio_temporal_voxel_layer. It clears by view
frustum: a voxel inside what the camera should be seeing, which no new
point re-marks, is removed in about 1 s, whatever is or is not behind it.
Voxels outside the frustum are kept: for 30 s after they were last seen in
the local map, indefinitely in the global one. The frustum must be set
inside the camera's real field of view, and STVL's FOV and range
parameters do not mean what they appear to; see
[TUNING](docs/TUNING.md#obstacle-detection).

The VoxelLayer grid also had a latent bug. `z_voxels: 20` exceeds the
16-voxel limit of a column (one 32-bit word), was clamped to 16 with only a
log line, ended the grid at 1.4 m instead of 1.8 m, and made clearing rays
above 1.4 m wrap round and wipe bits of the bottom voxels. STVL has no such
limit.

`min_obstacle_height: 0.10` is measured in the **costmap** frame, where
`base_link` is z = 0. Since `base_link` sits 0.10 m above the ground, that
threshold is 0.20 m above the floor. It is not a camera height. Anything
shorter than 20 cm, a hammer lying by the wheels for instance, is invisible
to the costmap, and lowering the threshold to see it is only safe once
`camera_pitch` has actually been measured.

### A blind camera must stop the rover

`expected_update_rate: 2.0` on both observation sources is new, added
2026-09-04. The old value was 0.0 by omission, which means Nav2 never
checks whether the camera is still alive: a wedged RealSense leaves the
last obstacles frozen in place and the rover drives on data that stopped
being true minutes ago, with no warning anywhere.

With it set, a cloud gap longer than two seconds makes the costmap report
itself not-current and the controller refuses to drive. The cloud arrives
at 7.4 Hz, so two seconds is a wide margin. This is the correct response to
a blind rover, but it does change the failure mode: a flaky camera now
stops the rover instead of silently risking it.

## Where the camera is bolted, and why it decides everything

Everything above assumes the costmap knows where the depth points came
from. That knowledge is three numbers in `urdf/athena.urdf.xacro`, and the
filter and the costmap simply believe them. They are load-bearing in a way
that no amount of Nav2 tuning can compensate for.

| Property | Value | How it was established |
|---|---|---|
| `camera_x` | 0.50 | tape, 2026-09-03. Lens is 0.15 m back from the front face |
| `camera_z` | 0.55 | tape, 2026-09-03. Lens is 0.65 m above ground, minus `base_height` 0.10 |
| `camera_pitch` | 0.0 | mounted level, in normal landscape, 2026-09-03 |
| `imu_link` | (0.50, 0, 0.40), rpy 0 0 0 | same place as the camera, 15 cm lower |
| `gps_link` | (0, 0, 0.25) | **assumed**, not measured |

Only the *orientation* of `imu_link` affects navigation, because no
accelerometer channel is fused; the EKF rotates the gyro into `base_link`
with it. The translation is written honestly anyway so nobody has to
re-derive it. `imu_rpy` being zero is an assertion that the board is bolted
down flat with its forward arrow pointing at the front of the rover. A
Pixhawk mounted upside down reports yaw rate with the wrong sign and the
rover turns *away* from its goal, harder the more it tries.

### The two errors that were live until 2026-09-03

**`camera_x` was 0.10**, which is 0.40 m behind where the lens actually is.
Every depth point was therefore marked that much closer to the rover than
it really was, so returns from just past the front bumper landed *inside*
the Nav2 footprint, and the controller read them as a collision it could
not drive out of.

**`camera_pitch` was -0.10.** In ROS, positive pitch is nose **down**, so
that value claimed a 5.7 degree *upward* tilt on a camera that has always
been level. Getting that sign backwards is most of the confusion in this
file's history.

An incorrect pitch rotates every depth point, and unlike a translation
error, the effect grows with range. With -0.10 the floor 2 m ahead of the
lens landed at z = +0.10 m in `base_link` instead of -0.10 m. That is
exactly `min_obstacle_height`. So flat ground from about 2 m out was marked
**lethal**, in a band right across the camera's field of view.

Together the two errors put that phantom band about 2 m in front of the
bumper. The controller refused to drive into it, Nav2 exhausted its
retries, and fell through to the stock Spin recovery, which turns 1.57 rad
counter-clockwise. That, and nothing more exotic, is the entire
long-running "the rover turns 90 degrees left" report.

### Why it took so long to find

Every diagnostic the stack had said the transforms were fine, because they
*were* fine: consistent, connected, correctly oriented. `tf_check` verifies
that the optical frame follows REP-103, that gravity points the right way,
that the cloud lands in +x. None of those notice that a translation is
0.40 m wrong, because none of them knows what the translation should be.

The fix was a tool that does not read the URDF at all.
`indoor_test/mount_check.py` RANSAC-fits the floor plane in the camera's
own optical frame and works out where the camera must be for that plane to
be the floor. It reports the mounting the hardware actually has, so it
stays honest no matter what the URDF currently claims, which matters
because that file had been edited back and forth several times on the
strength of readings that *did* depend on it.

Measured with it on 2026-09-04: pitch **-1.25 degrees**, roll **+0.52
degrees**. Both small enough to leave at zero.

Its `watch` mode turns all of this into the one number that matters,
continuously: where flat ground 3 m ahead is landing relative to
`min_obstacle_height`. Extrinsics do not drift on their own, so this is not
a calibration loop. What it catches is someone knocking the mount, or
editing the URDF, or the rover pitching on rough ground, and the floor
quietly starting to mark as a wall.

It supersedes `indoor_test/ground_check.py`, whose suggested `camera_z` is
computed against a hardcoded 0.20 / 0.30 m baseline from an older mounting.
That script now prints confident, wrong advice.

## Chain 2. Where am I?

Three sensors, none of which is sufficient alone:

| Sensor | Good at | Bad at |
|---|---|---|
| Camera (visual odometry) | smooth, precise short-term motion | drifting over time; blank walls |
| IMU | fast rotation (rate gyro) | drifts badly if you integrate it. Its *absolute* attitude on this FMU is not usable at all |
| GPS | absolute position that never drifts | noisy, ±3.5 m, needs sky |

The trick is to combine them so each covers the others' weakness:

```mermaid
flowchart TB
    CAM["camera"] --> VO["visual odometry<br/>how fast am I moving?"]
    VO --> GATE["vio_gate<br/>reject impossible motion"]
    PX["Pixhawk"] --> BR["pixhawk_bridge<br/>convert axes,<br/>compute covariance"]

    GATE --> L["FILTER 1 - local<br/>camera + IMU<br/>SMOOTH, never jumps"]
    BR -->|"IMU"| L
    GATE --> G["FILTER 2 - global<br/>same, plus GPS<br/>ACCURATE, may jump"]
    BR -->|"IMU"| G
    BR -->|"GPS"| NT["navsat_transform<br/>lat/lon to metres"]
    NT --> G

    L --> LO["/odometry/local<br/>used by local costmap"]
    G --> GO["/odometry/global<br/>used for waypoints"]
```

### Why two filters instead of one

This is the part that confuses people, and it is the heart of the design.

A navigation stack needs two different, **incompatible** things from a pose
estimate:

- **Smoothness.** The local costmap and the controller need a pose that
  never teleports. A sudden jump would smear obstacles across the map and
  make the rover swerve.
- **Absolute accuracy.** Waypoints are real places in the world. Without
  GPS the estimate slowly drifts away from reality.

You cannot have both in one estimate, because GPS corrections *are* jumps.
So the stack runs two filters on the same sensors:

- **Filter 1 (local)** never sees GPS, so it can never jump. It drifts
  slowly, and that is fine. Everything using it cares about *relative*
  geometry over a few metres.
- **Filter 2 (global)** adds GPS. When GPS corrects, this filter absorbs
  the jump by shifting the *relationship* between the map and the rover's
  local world, leaving the local estimate untouched.

That is what the `map → odom → base_link` transform chain encodes. Filter 2
owns `map → odom`; filter 1 owns `odom → base_link`. A GPS correction moves
the first link only.

```mermaid
flowchart LR
    map -->|"filter 2 - GPS<br/>absorbs jumps"| odom
    odom -->|"filter 1 - camera + IMU<br/>always smooth"| base_link
    base_link --> base_footprint
    base_link --> camera_link
    base_link --> imu_link
    base_link --> gps_link
```

`base_link` is the **parent** of `base_footprint`, not the child, which is
the opposite of most URDFs. `ekf_local` publishes `odom -> base_link`, so
declaring `base_footprint -> base_link` as well would give `base_link` two
parents. TF2 requires exactly one, and the result is that `base_footprint`
gets orphaned and every lookup involving it throws `ConnectivityException`.
Nothing here uses it, since Nav2 is configured with
`robot_base_frame: base_link`, but the upstream Nav2 GPS demo does, so a
config copied across would fail for no visible reason.

Six wheel links and a `nose_marker` hang off `base_link` too. They are
cosmetic; nothing reads them. Twelve links in total. There are no mast
frames: `camera_mast` and `gps_mast` were deleted on 2026-09-03 when the
sensors were mounted directly to the chassis.

### Two details that matter

**Visual odometry is fused as *speed*, not position.** The filter is told
"the rover is moving at 0.3 m/s", never "the rover is at x = 4.2 m". Visual
odometry resets itself when it loses tracking; if its position were fused,
every reset would yank the estimate. Feeding speed means a reset costs
nothing.

There is deliberately **no Mahalanobis gate** on that input
(`odom0_twist_rejection_threshold` is unset in both filters). Such a gate
self-locks: one accepted spike drives the state away, and then every honest
measurement looks like an outlier and is rejected forever. On the bench
that produced a 1.7 m/s phantom runaway. Physical outlier rejection lives
in `vio_gate` instead, where it can be reasoned about in m/s rather than in
standard deviations.

**Absolute heading is not fused at all any more.** This changed on
2026-09-02 and it is the design decision most likely to surprise you.

Historically the compass went into filter 2 only, because feeding heading
corrections at IMU rate into the smooth filter measurably pumped position
jitter, and REP-105 explicitly permits the odom frame to drift slowly in
heading. Filter 1 has always taken *turn rate* only.

Then the compass itself turned out to be unusable. With the rover sitting
flat, the FMU's attitude quaternion decodes to roll -22.3 degrees / pitch
-15.4 degrees, and the values are not consistent between sessions: 27.5
degrees on 2026-08-30, -21 / -17 on 2026-08-31. Fusing it anchored the map
frame's rotation to that, producing a permanent `map -> odom` yaw of +89
degrees while the rover was plainly not pointing north, so every goal given
in absolute map coordinates was aimed about 90 degrees away from where the
operator meant it.

So index 5 is now false in **both** filters, and only the yaw rate at index
11 remains. A rate gyro's output does not depend on the broken attitude
solution, which is what makes this survivable. It is also what keeps the
EKFs running near 20 Hz instead of 7 to 8.

The consequence is that map yaw is dead-reckoned: `map` and `odom` agree in
rotation and drift together. Correct for the odom-frame goals this rover
drives today, **not** sufficient for GPS waypoint work, which needs a real
absolute heading again: index 5 re-enabled against a calibrated compass,
or, better, a dual-antenna RTK heading. `navsat_transform`'s
`use_odometry_yaw` is still `false`, so it also still reads `/imu/data` yaw
for the datum heading. Both want fixing together.

## Indoors: one filter, not two

`bringup.launch.py local_only:=true` drops `ekf_global` and
`navsat_transform` and publishes a static identity `map -> odom` in their
place.

Nav2's configuration is left exactly as it is for GPS work. `global_frame`
stays `map` everywhere, because with that static transform `map` **is**
`odom`, exactly, by construction. Nothing has to be rewritten and switching
back is just dropping the flag.

The point is not to save CPU. Everything above about the two filters
assumes filter 2 has something filter 1 does not: GPS. With no fix it does
not. It dead-reckons the same VIO and the same gyro that `ekf_local`
already does, and two independent filters on identical inputs do not stay
identical: their estimates slowly diverge for no physical reason at all.

That divergence *is* the `map -> odom` drift you see indoors. It is not
information, it is numerical disagreement between two copies of the same
sum. Delete the second filter and it cannot happen. Identity is the honest
value for `map -> odom` here, because with no GPS there is nothing anywhere
in the system that could distinguish the two frames.

`pixhawk_bridge` still runs and still publishes `/gps/fix`, so the receiver
can be watched acquiring without anything fusing it. `stack_check` reports
`EKF global (map)` and `navsat gps->map` as FAIL in this mode, correctly:
those nodes are not running.

## How it decides to move

The planner is **NavFn** on the global costmap: Dijkstra by default
(`use_astar: false`), `allow_unknown: true` because a rolling window with
no prior map is mostly unknown, and a 1.0 m goal tolerance to match a
±3.5 m position sensor.

The controller is **Regulated Pure Pursuit**, chosen over MPPI because it
is cheap on a Jetson already carrying visual odometry and a camera driver.
It picks a "carrot" on the path a fixed distance ahead and steers at it.

### Why the lookahead is fixed, not velocity-scaled

This is the second half of the "rover yaws instead of driving" bug, and it
is a genuinely nasty interaction.

RPP's velocity-scaled mode computes
`lookahead = clamp(|speed.linear.x| * lookahead_time, min, max)`. Speed is
zero at the moment every goal starts, so the carrot pins to
`min_lookahead_dist`, which was 0.4 m. The rover's own footprint reaches
x = +0.65, so a 0.4 m carrot sits **inside the robot**. NavFn snaps the
path start to a 0.1 m grid cell, and that snap alone put the carrot at
-0.58 rad, past `rotate_to_heading_min_angle` (0.5), so RPP zeroed
`linear.x` and turned in place.

It could never recover, because building speed is precisely what would have
lengthened the lookahead. Chicken and egg. Measured on a 2 m goal down a
clear corridor:

| | forward command |
|---|---|
| velocity-scaled, 0.4 m carrot | `linear.x` = 0.000 on 160 of 160 cycles |
| fixed 1.0 m carrot | `linear.x` = 0.350 on 178 of 178 cycles |

So `use_velocity_scaled_lookahead_dist` is **false** and `lookahead_dist`
is a flat 1.0 m, which keeps the carrot clear of the footprint with margin.
Velocity scaling buys very little on a rover whose entire speed range is 0
to 0.35 m/s. `min_lookahead_dist` was raised to 0.9 and `max` to 1.5 even
though both are now unused, so that re-enabling scaling cannot silently
reintroduce a carrot inside the robot.

### Why `odom_topic` has to be set three times

The other half of the same bug. Nav2's default `odom_topic` is the bare
topic `odom`, which nothing in this stack publishes: `ekf_local` publishes
`/odometry/local`. With no publisher, `controller_server`'s `OdomSmoother`
reports speed 0.0 forever, which is what pinned the lookahead at its
minimum in the first place.

`bt_navigator` and `velocity_smoother` were already pointed at
`/odometry/local`. `controller_server` was the one that was missed, and it
was the one that mattered.

### Turning slowly is a perception decision, not a comfort one

`rotate_to_heading_angular_vel` is 0.4 rad/s, down from 0.8, and
`behavior_server`'s `max_rotational_vel` is 0.5, down from 0.8.

The reason is not the motors. VIO runs about 10 Hz outdoors and collapses
to 2 to 4 Hz indoors. At 0.8 rad/s the rover sweeps 12 to 25 degrees
between pose updates, and every cloud arriving in that gap is placed into
the costmap with a stale heading. At 3 m range that smears an obstacle by
up to 0.8 m. Smear the camera can still see clears in about a second, but
smear it has looked away from stays marked until it expires (30 s in the
local map, never in the global one). Turning in place is exactly when
this is worst, which is why the two rotation limits are the ones that got
halved.

`velocity_smoother`'s angular ceiling came down from 1.2 to 0.6 for the
same family of reasons: nothing upstream asks for more than 0.5, and a
ceiling far above what anything requests only matters when something
misbehaves, at which point it lets it misbehave fast.

## Recovery: why Spin and BackUp were removed

Athena runs its own behaviour tree,
`behavior_trees/athena_nav_to_pose.xml`, selected by `bt_navigator`'s
`default_nav_to_pose_bt_xml`. It is Nav2's stock
`navigate_to_pose_w_replanning_and_recovery.xml` with two recovery
behaviours deleted.

The main branch is unchanged: replan at 1 Hz, follow the path, each
retrying once on its own before the whole thing drops into recovery.

**The stock recoveries assume a robot that can see where it is about to
move.** Athena cannot. The D435i covers 87 degrees ahead and there is no
rear-facing sensor at all:

| Stock recovery | What it actually does here |
|---|---|
| `Spin(1.57 rad)` | rotates the rover through 273 degrees it cannot see, using costmap cells last observed some time ago and, with VIO at 2 to 4 Hz indoors, written with a heading that was already stale |
| `BackUp(0.30 m)` | reverses a 1.3 m rover into space it has **never** observed. There is no sensor pointing that way. It is not a cautious move, it is a blind one |

What remains is the recovery that is both safe and actually effective:
clear both costmaps, then `Wait 5`, round-robin, up to 6 rounds, then fail
the goal cleanly. That covers the common real failures on this rover, a
stale costmap, a transient VIO dropout, a camera hiccup now that
`expected_update_rate` can invalidate an observation, without moving blind.
Anything those do not fix hands control back to the operator, which on a
rover with a 273 degree blind arc is the correct outcome.

There is a diagnostic bonus. Stock `Spin(1.57 rad)` is exactly 90 degrees
counter-clockwise, and that unmistakable signature is what the
long-standing "rover turns 90 degrees left" symptom always was: not a
steering bug, but Nav2 correctly reporting that the controller could not
produce a command. With the Spin gone, the same underlying failure now
presents as the rover sitting still, which is both safer and much easier to
read.

The `spin` and `backup` plugins are still loaded by `behavior_server` and
still listed in `plugin_lib_names`, so nothing calls them but nothing has
to be rebuilt differently either. Reverting is deleting one line from
`nav2_params.yaml`.

## From sensor to motor, end to end

The full picture, once you know what each half does:

```mermaid
flowchart TD
    CAM["D435i"] --> RS["camera driver"]
    PX["Pixhawk"] --> PB["pixhawk_bridge"]

    RS -->|"depth cloud"| DS["downsampler"]
    RS -->|"images + camera IMU"| VO["visual odometry"]
    VO --> GATE["vio_gate"]

    DS --> LC["local costmap"]
    DS --> GC["global costmap"]

    GATE --> EL["filter 1 (local)"]
    GATE --> EG["filter 2 (global)"]
    PB -->|"/imu/data"| EL
    PB -->|"/imu/data"| EG
    PB -->|"/gps/fix"| NT["navsat_transform"]
    NT --> EG

    EL -->|"odom to base_link"| LC
    EG -->|"map to odom"| GC

    LC --> CTRL["controller<br/>Regulated Pure Pursuit"]
    GC --> PLAN["planner<br/>NavFn"]
    PLAN --> CTRL
    CTRL --> MB["motor bridge"]
    MB --> MOT["Pico W to 6 motors"]
```

## Hardware

| Device | Connection | Read by |
|---|---|---|
| RealSense D435i | USB 3 (`8086:0b3a`) | `realsense2_camera_node` |
| Pixhawk PX4 FMU v2 | USB CDC (`26ac:0011`), MAVLink **@921600** | `pixhawk_bridge` |
| Raspberry Pi Pico W | USB CDC (`2e8a:f00a`) | `athena_drive/motor_bridge` |

Always address serial devices by their `/dev/serial/by-id/...` path. The
`ttyACM*` numbers shuffle between boots, and the old `athena_slam` scripts
hard-code `/dev/ttyACM0`, which is usually the **Pixhawk**, not the motors.

`camera_link → camera_camera_link` in the frame tree is a static identity
bridge: realsense-ros roots its own frames at `<camera_name>_camera_link`
and ignores `base_frame_id`, so without it the camera frames float free of
the robot and visual odometry cannot start.

## When a sensor drops out

| Lost | What happens |
|---|---|
| **GPS** | The map frame stops being corrected. Obstacle avoidance, the local costmap and the odom frame all keep working. |
| **Visual odometry** | The filter coasts on the IMU; VO resets itself and rejoins. |
| **Camera** | For up to 2 s, no new obstacles are marked and the costmap keeps what it already saw. Past `expected_update_rate` the costmap declares itself not-current and the **controller stops driving**. Deliberate: a rover that cannot see should not move. |
| **Pixhawk** | No yaw rate and no GPS; the camera alone still gives a usable local pose. Absolute heading is not fused even when the Pixhawk is healthy. |
| **`/cmd_vel`** | Motor bridge stops the motors after 0.5 s; the Pico firmware independently stops them 0.5 s later. |

---

---

# Every file in this package

## The nodes that run all the time

These three are live whenever the rover is on. Everything else is a tool
you run by hand.

| File | What it does |
|---|---|
| `pixhawk_bridge.py` | Talks MAVLink to the Pixhawk and publishes `/imu/data` and `/gps/fix`. Converts aviation axes (north-east-down) into ROS axes (east-north-up), and turns the GPS's HDOP number into an honest covariance so the filter knows how much to trust it. Runs the link at 921600 baud: at 115200 a third of the frames arrive corrupted. Also removes an online-estimated gyro bias. |
| `vio_gate.py` | Sits between visual odometry and the filters and throws away motion the rover cannot have made: someone walking past the camera reads as the world moving. Also forces an exact zero when `/cmd_vel` says the rover is parked, which is what keeps stationary drift at zero. |
| `pointcloud_downsampler.py` | Thins the ~77,000-point depth cloud to ~4,300 by keeping every 8th point within 0.25 to 3.5 m, so the costmap update stays cheap enough for a Jetson. |

## Tools you run when something looks wrong

| File | Answers the question |
|---|---|
| `stack_check.py` | "Is the whole chain healthy?" One PASS/FAIL line per stage, including a physics check that the IMU's reported attitude agrees with the gravity it measures. |
| `tf_check.py` | "Are the transforms *oriented* right, not just present?" A tree can look perfect in RViz and still have the camera rotated 90°. This checks gravity points up in `base_link` at rest, the cloud lands in front, and the optical frame follows the standard rotation. It does **not** know what any translation should be, which is why it never caught the `camera_x` error. |
| `localization_monitor.py` | "How much does the pose drift?" Records for N seconds and writes an accuracy report to `~/athena/loc_reports/`. |
| `costmap_drift_check.py` | "Does the costmap slide when nothing is moving?" |
| `gps_diagnose.py` | "Why does GPS have no fix?" Talks to the Pixhawk directly and reports fix type, satellite count and HDOP. Not a ROS node: plain `argparse`, so `--seconds`, not `-p seconds:=`. Needs exclusive access to the serial port, so stop the stack first. |
| `gps_waypoint_logger.py` | "Can I record this route by driving it?" Press Enter at each spot to save a waypoint. |
| `gps_waypoint_follower.py` | "Can it drive that route back?" Humble's Nav2 has no GPS waypoint action, so this converts each lat/lon itself through `/fromLL` and feeds Nav2 ordinary map-frame goals. Run by hand, not by `bringup`. |
| `fake_gps_imu.py` | "Can I test with no hardware at all?" Publishes synthetic sensors for `bench_test.launch.py`. |

Those eleven, plus the three above, are the complete set of
`ros2 run athena_gps_nav` entry points declared in `setup.py`.

### Tools that live outside this package

`indoor_test/mount_check.py` is not part of `athena_gps_nav` and is not a
`ros2 run` target: it is a standalone script, run as
`python3 ~/athena/indoor_test/mount_check.py <camera|costmap|yaw|watch>`.
It lives outside the package because it deliberately does not depend on the
package's own view of the world; see
[Where the camera is bolted](#where-the-camera-is-bolted-and-why-it-decides-everything).
It supersedes `indoor_test/ground_check.py`, which is now wrong.

## Launch files

Each one starts a layer. `bringup` starts them all in order; the others exist
so you can bring up one layer at a time when debugging.

| File | Arguments | Starts | You get |
|---|---|---|---|
| `sensors.launch.py` | `use_camera` | camera, camera IMU filter, Pixhawk bridge, downsampler, robot description | raw sensor topics and the TF tree |
| `vio.launch.py` | none | rtabmap visual odometry, `vio_gate` | `/vio/odometry` |
| `localization.launch.py` | `use_sim_time`, `local_only` | both EKFs, `navsat_transform`, or one EKF plus a static `map → odom` | `/odometry/local`, `/odometry/global`, `map → odom → base_link` |
| `navigation.launch.py` | `use_sim_time` | Nav2, via `nav2_bringup/navigation_launch.py` | costmaps, planner, controller |
| `bringup.launch.py` | `dry_run`, `use_camera`, `foxglove`, `local_only` | all of the above, plus motors and the Foxglove front end | the whole rover, one command |
| `bench_test.launch.py` | none | fake sensors plus the real pipeline | the stack with no hardware attached |

Those are the only arguments declared; `--show-args` on any of them is the
authoritative list. `bringup` passes `use_camera` down
to `sensors`, gates `vio` on it, passes `local_only` down to
`localization`, and passes `dry_run` to `athena_drive`.

The staggering is not cosmetic: VIO at +5 s so the camera streams exist,
localization at +8 s, Nav2 at +12 s, and the operator front end at +15 s,
because it only serves what already exists and starting it early just means
a panel full of missing topics.

`sensors.launch.py` launches the RealSense driver by **absolute path** to
`/opt/ros/humble/lib/realsense2_camera/realsense2_camera_node` rather than
by package name. This machine also carries an unrelated rover project at
`~/ros2_ws` with its own from-source `realsense2_camera`, and `~/.bashrc`
sources it, so package-based resolution silently picks whichever build is
first on `AMENT_PREFIX_PATH`. That was found on 2026-08-31 after camera
orientation bugs kept reappearing despite a correct URDF: the running
binary was the wrong one.

`navigation.launch.py` wraps `nav2_bringup`'s own launch file. That matters
for one reason: `nav2_bringup` builds the parameter file with
`allow_substs=True`, which is what lets `nav2_params.yaml` write
`$(find-pkg-share athena_gps_nav)/behavior_trees/athena_nav_to_pose.xml`
instead of an absolute path.

## Configuration

| File | Holds |
|---|---|
| `config/dual_ekf_navsat.yaml` | Both filters and the GPS transform. The sensor-to-filter matrix lives here: which of the fifteen state variables each sensor is allowed to correct. |
| `config/nav2_params.yaml` | Costmap layers, obstacle ranges, planner and controller tuning, and the pointer to the behaviour tree below. |
| `behavior_trees/athena_nav_to_pose.xml` | The navigate-to-pose tree, stock minus the Spin and BackUp recoveries. See [Recovery](#recovery-why-spin-and-backup-were-removed). |
| `config/athena_bench.rviz` | An RViz layout with the useful displays already added. |
| `config/waypoints_example.yaml` | The file format `gps_waypoint_follower` expects. |
| `urdf/athena.urdf.xacro` | Where the sensors sit on the rover, and the shape drawn in 3D views. The offsets are load-bearing: the filter believes them. |

With `--symlink-install`, all six are symlinked from `install/` through
`build/` back to `src/`, so **editing** one takes effect on the next
relaunch with no rebuild. **Adding** a file does need a rebuild, because
the symlink has to be created: that is why `behavior_trees/` required one
when it first appeared. `colcon build` without the flag copies instead, and
then every later edit is silently ignored.

# What this differs from, and why

Two existing packages were the starting point. Both were kept as reference
and neither worked as-is on this rover. The reasons are worth recording,
because each one is a trap that looks like it should work.

## Reference 1. The official Nav2 GPS demo (`~/gps_nav_ws`)

`nav2_gps_waypoint_follower_demo` is the upstream example this stack's
architecture comes from. The dual-EKF + `navsat_transform` design is taken
from it deliberately and unchanged in spirit. Three things stopped it
running here.

**It has no source of translation.** Its local EKF fuses only the IMU:

```yaml
imu0_config: [false, false, false,    # x  y  z    - no position
              false, false, true,     # roll pitch yaw
              false, false, false,    # vx vy vz   - no linear velocity
              true,  true,  true,     # angular rates
              false, false, false]    # accelerations
```

Nothing in that list tells the filter the robot moved *forward*. Upstream
that is fine, because the demo robot has wheel encoders feeding a separate
odometry source. **Athena has no wheel encoders at all.** Copied verbatim,
the local EKF can only observe rotation: drive ten metres and the odom
frame still reports you standing still, which makes the local costmap
meaningless. That gap is exactly what visual odometry fills here.

**Its Nav2 config targets a newer Nav2.** The demo's params reference
`docking_server` (needs `opennav_docking`), `loopback_simulator`,
`nav2_route`, `error_code_name_prefixes` and `enforce_path_inversion`.
None of which exist in Humble's Nav2 1.1.20. It also runs MPPI, which is
heavy for a Jetson already carrying visual odometry and a camera driver.

**Its GPS covariance is nominal, not measured.** Fine for simulation with
clean synthetic noise; on real hardware it under-reports error by ~1.8x at
good HDOP. See [the error model](docs/TUNING.md#how-hard-gps-pulls-the-map).

## Reference 2. The earlier `athena_slam` package

The MAVLink reading approach came from here. Its remaining nodes are kept
for reference but should not be used for navigation.

**Wrong axes.** `gpsimusplit.py`, `imupub.py` and `gpspub.py` publish
MAVLink values straight through:

```python
imu.linear_acceleration.y = ay        # no negation
imu.angular_velocity.z   = gz         # no negation
qx, qy, qz, qw = self._euler_to_quat(att.roll, att.pitch, att.yaw)   # raw NED yaw
```

MAVLink reports body rates in FRD (forward-right-**down**) and attitude
against NED, where yaw 0 means North and increases clockwise. ROS expects
FLU (forward-left-**up**) and ENU, where yaw 0 means East and increases
counter-clockwise. Publishing one as the other violates REP-103: gravity
points the wrong way, turns register backwards, and `navsat_transform`,
which uses IMU heading to align GPS with the map. Builds its transform
from a heading that is mirrored and rotated 90 degrees. `pixhawk_bridge`
converts both properly.

**Wrong baud.** `imupub.py` and `gpspub.py` use 115200. Measured on this
FMU that corrupts **33%** of MAVLink frames and yields ~11 usable IMU
samples per 18 s. At 921600 corruption is 0% and the IMU runs at tens of Hz
(39 Hz with the full stack up, 42 to 49 Hz on a quiet machine). Only
`gpsimusplit.py` had this right.

**Wrong device, hard-coded.** All three open `/dev/ttyACM0`. That number is
assigned in enumeration order and moves between boots. On this rover it is
usually the Pixhawk, which is why `drive/move.py` was sending motor
commands to the flight controller. Everything here uses
`/dev/serial/by-id/` paths, which are stable.

**Wrong message type.** `gpspub.py` publishes `geometry_msgs/Point` with
latitude in `x`. `navsat_transform` requires `sensor_msgs/NavSatFix`, and a
Point carries no covariance, so the filter has no way to know how much to
trust it.

## What was added that neither reference has

| | Why |
|---|---|
| Visual odometry as the translation source | no wheel encoders exist on this rover |
| `vio_gate` | VO reports motion that did not happen: a person walking past read as 0.75 m/s and produced a 93 cm jump |
| Zero-velocity update | stationary drift; no ZUPT exists in rtabmap's built-in odometry |
| Measured GPS error model | nominal covariance under-reports real error by 1.8x at good HDOP |
| Velocity-only VO fusion | VO resets would otherwise yank the pose every time tracking is lost |
| Yaw rate, never absolute yaw, in **both** filters | heading corrections at IMU rate cross-coupled into velocity and pumped position jitter; and then the FMU's attitude solution turned out to be wrong by tens of degrees anyway |
| A behaviour tree with no Spin and no BackUp | 87 degree camera, no rear sensor: both stock recoveries move the rover through space it cannot see |
| `local_only` | with no fix, a second EKF on identical inputs manufactures `map -> odom` drift out of nothing |
| Fixed rather than velocity-scaled lookahead | scaling pins the carrot inside the rover's own footprint at goal start, and it can never grow out of it |
| `expected_update_rate` on both costmaps | a wedged camera used to leave stale obstacles frozen in place with no warning |
| `stack_check`, `gps_diagnose`, `costmap_drift_check`, `tf_check`, `mount_check.py` | every failure above was silent; each needed a way to be seen |

---

---

# Verified results

Measured on the real rover. Each block says when. Reproduce them with the
commands in [docs/TESTING.md](docs/TESTING.md).
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

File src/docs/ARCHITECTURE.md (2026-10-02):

# Athena architecture

How the pieces fit: packages, data flow, frames, and the design decisions that
are not obvious from the code. To *run* the rover see the [root README](../README.md).
For depth on navigation see [athena_gps_nav/ARCHITECTURE.md](../athena_gps_nav/ARCHITECTURE.md).

Athena answers two questions with two chains that meet only in Nav2 (**where am
I?** and **what is around me?**), then acts on them. The separation is
deliberate: if GPS drops out, obstacle avoidance is untouched.

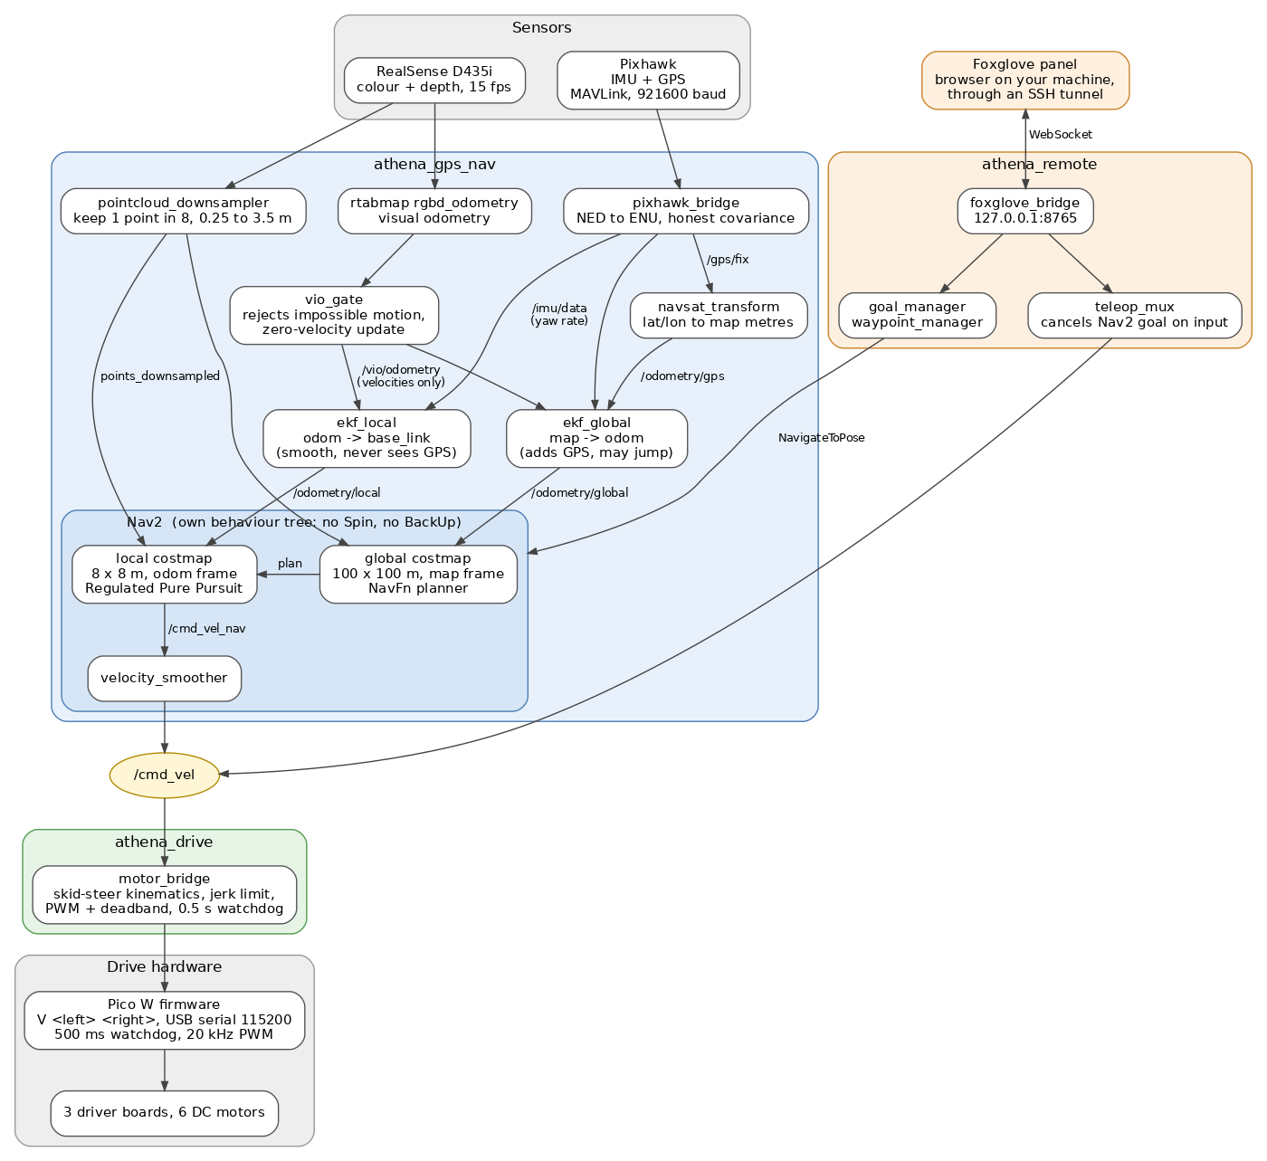
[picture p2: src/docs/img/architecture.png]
Athena data flow from sensors through localization and Nav2 to the motors

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

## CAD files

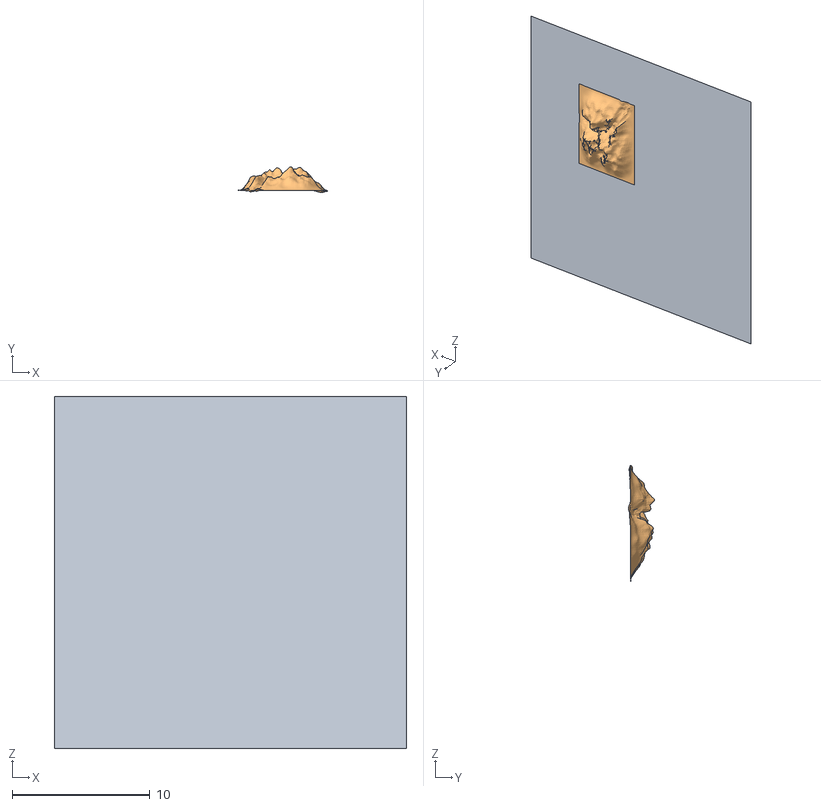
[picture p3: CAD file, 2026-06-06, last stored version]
src/drive/drive/mount.blend1.obj
25.5 x 1.93 x 25.5
Plane
Landscape

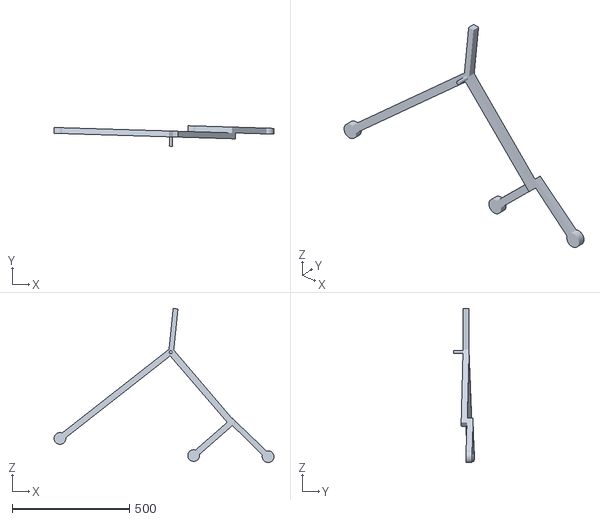
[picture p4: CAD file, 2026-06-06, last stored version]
src/rover_description/meshes/bogie_right_1.stl
938.6 x 88.0 x 657.1

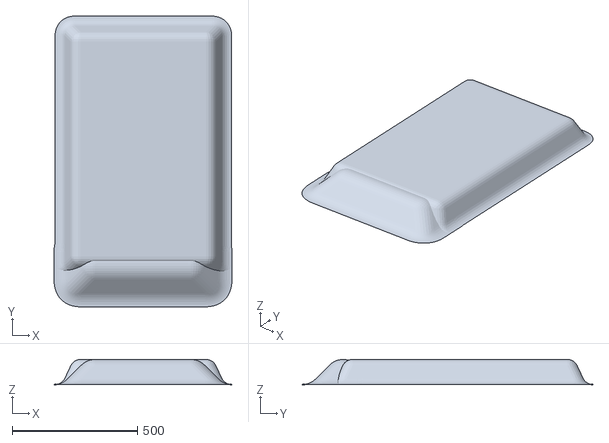
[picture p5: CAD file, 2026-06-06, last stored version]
terrain3.obj
709.5 x 1159.1 x 100.0

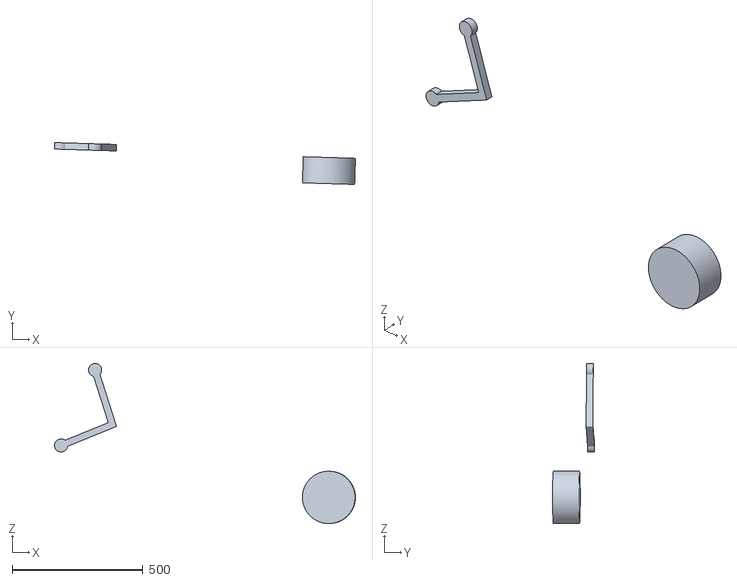
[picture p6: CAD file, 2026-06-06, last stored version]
src/rover_description/meshes/wheel_bl_1.stl
1150.1 x 160.1 x 611.7

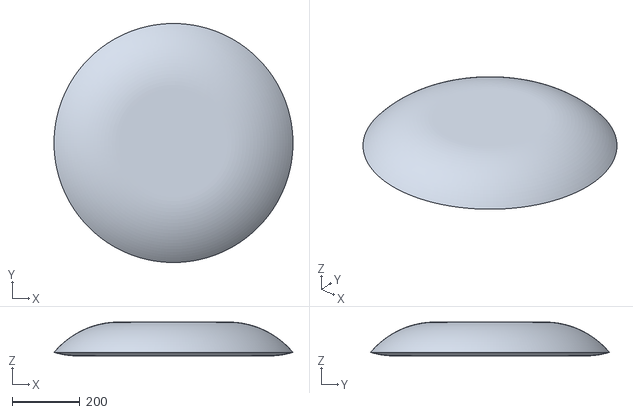
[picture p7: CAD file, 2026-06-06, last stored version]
terrain1.obj
703.2 x 703.2 x 100.0

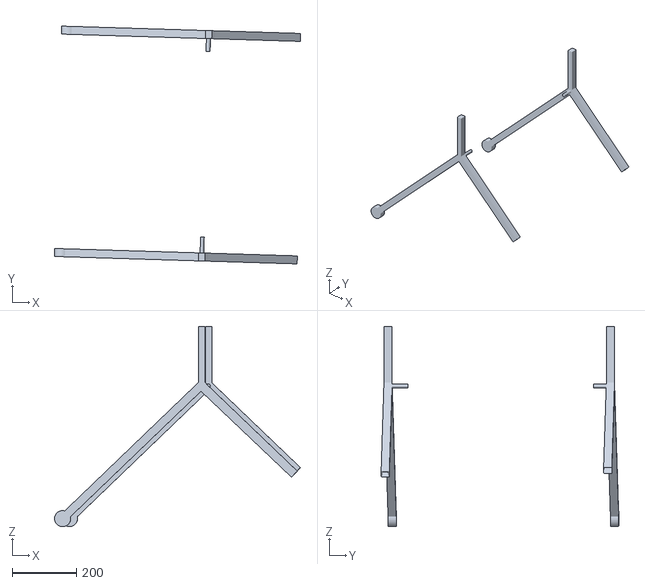
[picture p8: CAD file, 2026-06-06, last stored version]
src/rover_description/meshes/rocker_right_1.stl
768.5 x 742.9 x 625.4

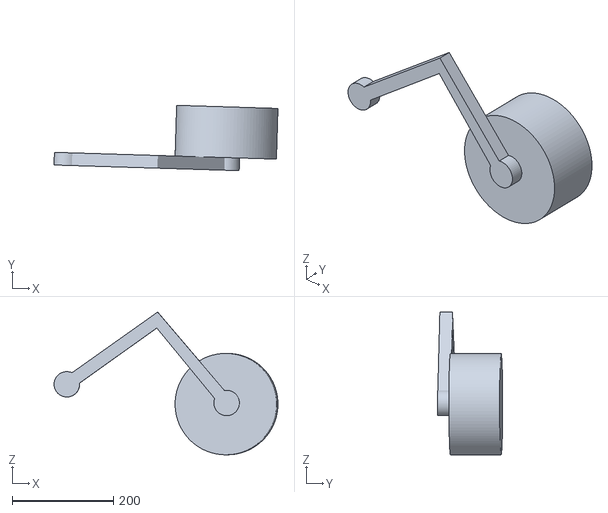
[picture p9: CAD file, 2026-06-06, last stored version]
src/rover_description/meshes/wheel_br_1.stl
441.7 x 128.8 x 281.3

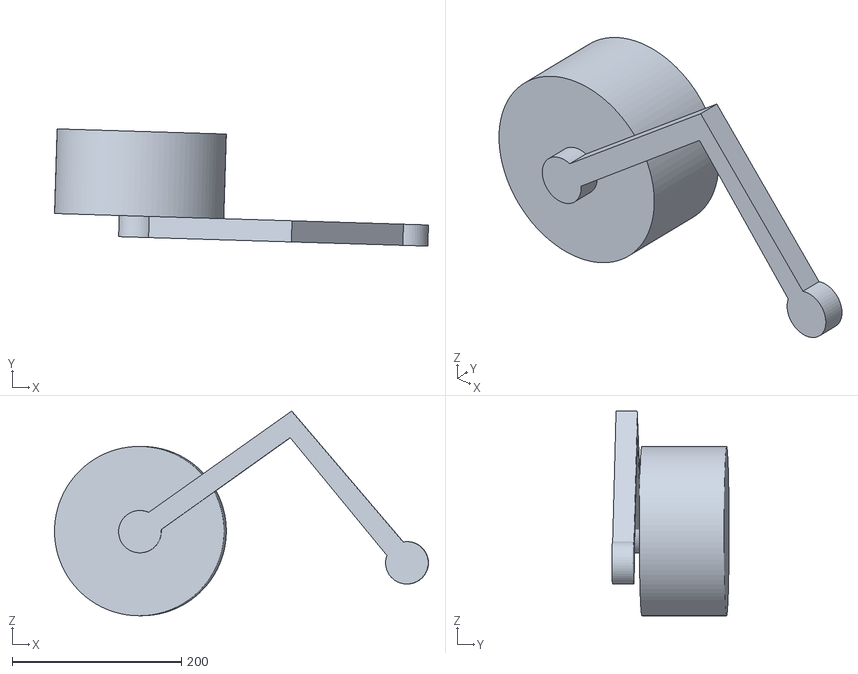
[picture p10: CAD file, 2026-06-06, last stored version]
src/rover_description/meshes/wheel_mr_1.stl
441.6 x 138.5 x 241.5

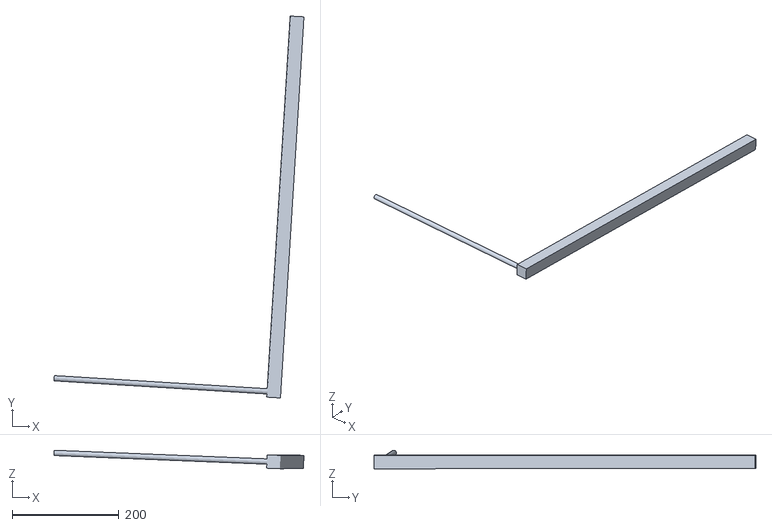
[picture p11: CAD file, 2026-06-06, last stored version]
src/rover_description/meshes/support_right_1.stl
468.0 x 715.2 x 34.7

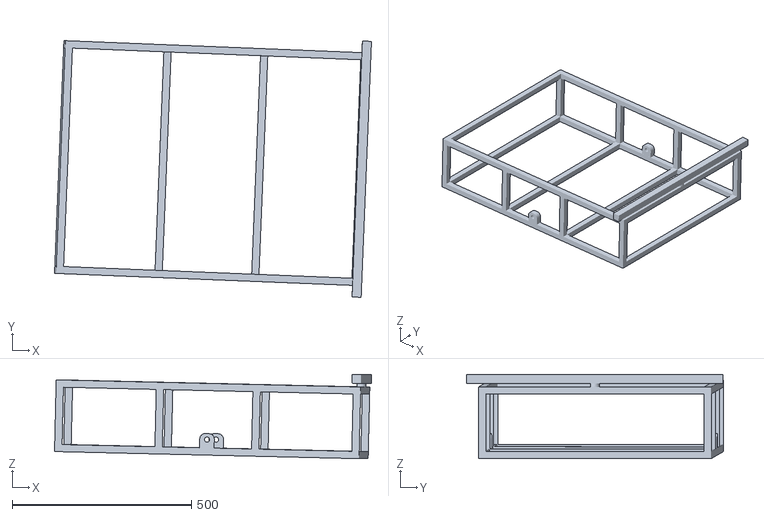
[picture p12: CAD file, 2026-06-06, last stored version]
src/rover_description/meshes/differential_bar_1.stl
884.6 x 716.5 x 235.6

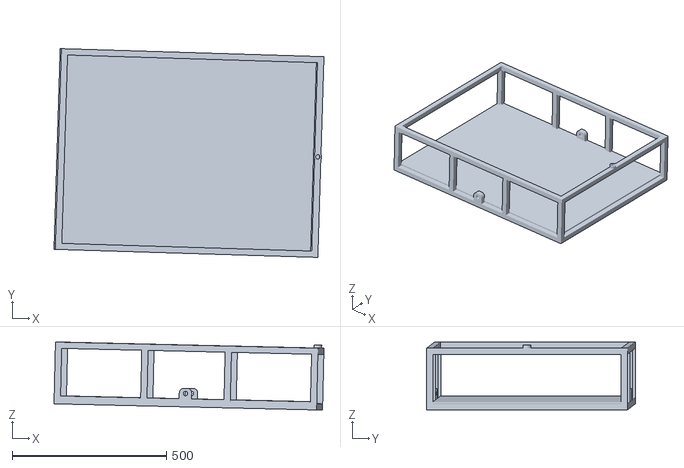
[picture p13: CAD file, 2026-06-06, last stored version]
src/rover_description/meshes/base_link.stl
873.9 x 675.8 x 219.8

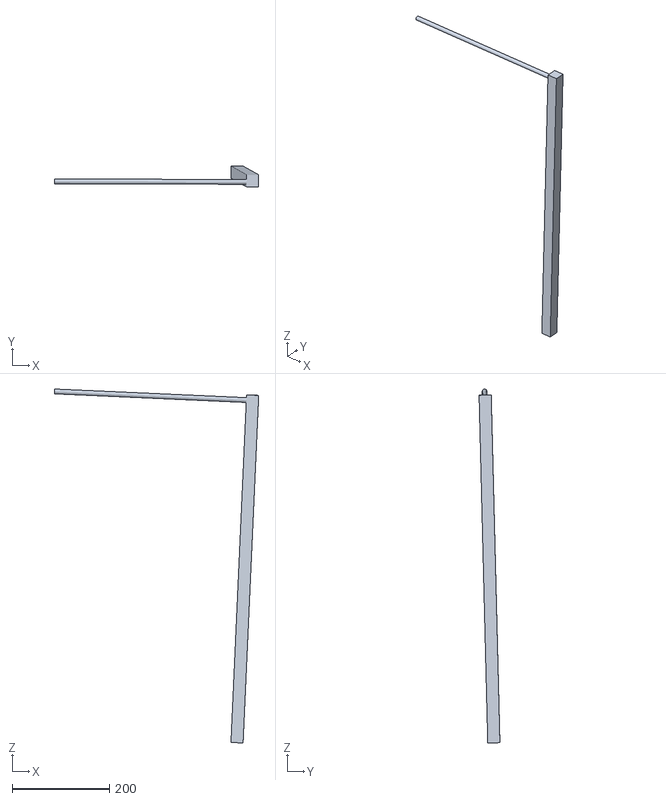
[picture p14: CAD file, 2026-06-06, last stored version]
src/rover_description/meshes/support_left_1.stl
420.3 x 42.9 x 727.6

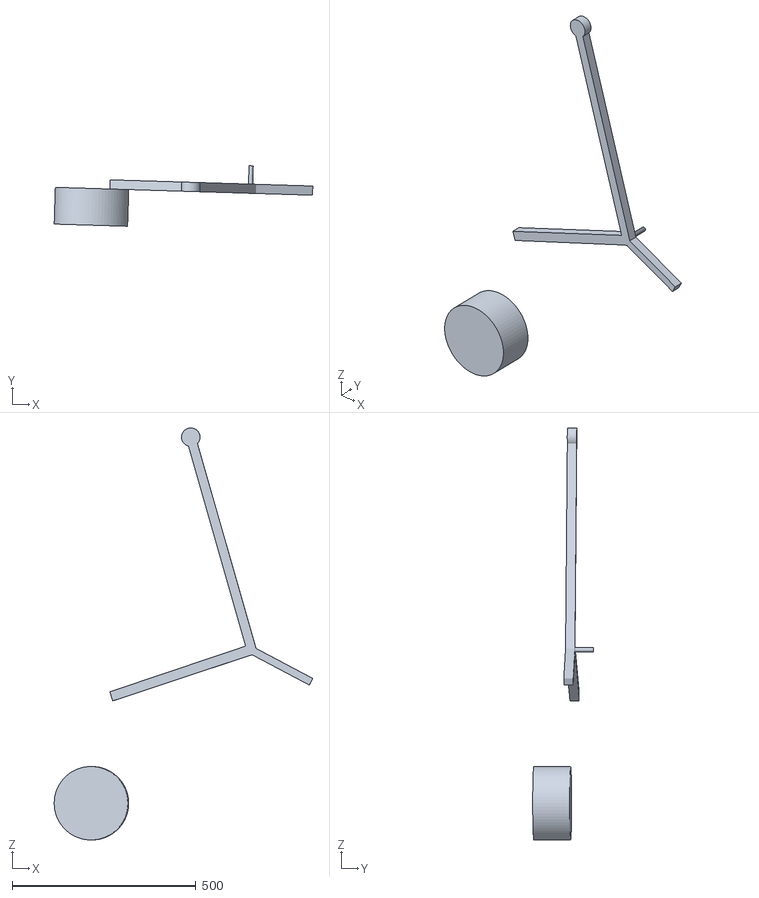
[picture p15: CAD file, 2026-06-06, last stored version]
src/rover_description/meshes/wheel_fl_1.stl
703.9 x 165.0 x 1121.1

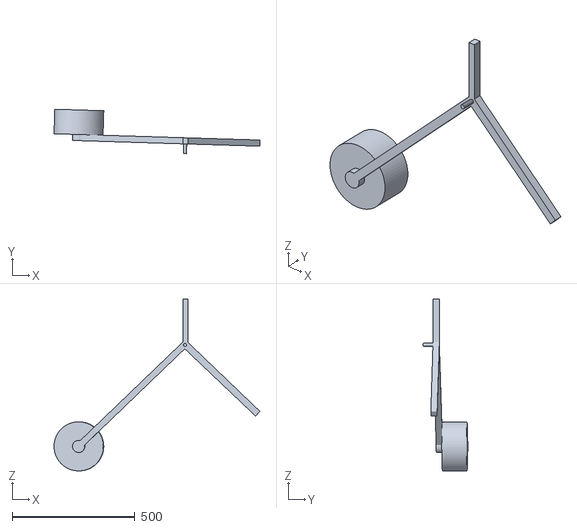
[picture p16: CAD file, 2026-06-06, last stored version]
src/rover_description/meshes/wheel_fr_1.stl
839.6 x 181.5 x 700.1

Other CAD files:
src/rover_description/meshes/rocker_left_1.stl
src/rover_description/meshes/wheel_ml_1.stl
src/rover_description/meshes/bogie_left_1.stl

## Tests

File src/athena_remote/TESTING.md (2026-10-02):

# Testing the nav stack from Foxglove

How to send a goal from Foxglove and tell, from the panel alone, *why* it did
what it did. [README.md](README.md) and [docs/FOXGLOVE_PANEL.md](docs/FOXGLOVE_PANEL.md) cover connecting; this covers testing.

Written 2026-09-02, after a session where the rover yawed instead of driving.
The diagnostic panels described here exist because that bug was invisible
without them.

---

## 0. Before you connect

One stack, and only one. Two `bringup.launch.py` instances on the same
`ROS_DOMAIN_ID` will each run their own `ekf_global` broadcasting `map -> odom`
and their own `ekf_local` broadcasting `odom -> base_link`, and TF flips
between two independent estimates at 30 Hz. The plan looks fine and execution
is garbage. It is not obvious from any panel.

```bash
ros2 node list | sort | uniq -c | awk '$1>1'
```

Any output at all means duplicates. Nothing printed is what you want.

Run that on the Jetson, or over ssh with the domain set explicitly —
`ssh robo@172.20.119.87 'export ROS_DOMAIN_ID=42; source ~/athena/install/setup.bash && ros2 node list'`.
A non-interactive shell returns early from `~/.bashrc` and lands on domain 0,
where the list is empty and every duplicate is invisible.

**The Pico's serial port is exclusive**, and bringup starts its own
`motor_bridge`. A second bridge, or a stray `calibrate` / `wiring_check` /
`calibrate_speed` left running, takes the port or fails to get it, and
either way `/cmd_vel` stops reaching the wheels. The only sign is one
`could not open ... - running dry` line at startup, which scrolls past in
the launch output; after that the node behaves exactly like a healthy one.
Check before launching:

```bash
fuser -v /dev/ttyACM*
```

Then:

```bash
ros2 launch athena_gps_nav bringup.launch.py
```

Bringup already includes the Foxglove bridge and the motor bridge. Give it
~45 s: sensors at t=0, VIO at t=5, localization at t=8, Nav2 at t=12, panel
at t=15.

Four arguments, and these are all of them: `dry_run`, `use_camera`,
`foxglove`, `local_only`.

---

## 1. Static checks, before anything moves

Do these in order. Each one takes seconds and each has caught a real fault.

**TF tree is a single chain.** In the 3D panel the rover model should appear
once, upright, with the cyan nose block pointing forward. From the shell:

```bash
ros2 run tf2_tools view_frames
```

You want exactly one root (`map`), one `map -> odom`, one `odom -> base_link`,
and every sensor hanging off `base_link`. 11 frames hang directly off
`base_link` (the six wheels, `base_footprint`, the nose marker, `camera_link`,
`imu_link`, `gps_link`; the two masts were deleted on 2026-09-03), and the
RealSense's own frames hang below `camera_link`. The total frame count (27 when
this was written, before the masts were removed) will be lower now: count with
`view_frames`.

**The footprint is the real one.** The 3D panel draws
`/local_costmap/published_footprint` in cyan. It should be a 1.3 m x 1.0 m
rectangle around the rover — *the footprint Nav2 is actually using*, not the
one you think is configured. It comes from
`footprint: "[[0.65, 0.5], [0.65, -0.5], [-0.65, -0.5], [-0.65, 0.5]]"` in
`nav2_params.yaml`. If it looks like a small square, the params did not
reload.

> **Check how your configs are actually installed before blaming a stale
> build.** On this workspace `install/.../config/*.yaml` is a symlink to
> `build/.../config/*.yaml`, which is itself a symlink to `src/`. So the
> chain lands in `src` and an edit there *does* take effect on the next
> node start, no rebuild needed. Confirm rather than assume:
>
> ```bash
> readlink -f ~/athena/install/athena_gps_nav/share/athena_gps_nav/config/nav2_params.yaml
> ```
>
> If that prints a path under `src/`, editing is enough. If it prints a path
> under `build/` (a plain `colcon build`, no `--symlink-install`), you have
> a real copy and the edit changes nothing until you rebuild. Adding a
> *new* config file always needs a rebuild either way: the `glob()` in
> `setup.py` runs at build time.

**Odometry is not running away while parked.** Watch the *Speed* tab with the
rover stationary. `measured m/s` and `measured rad/s` should sit on zero. Any
sustained non-zero reading on a parked rover is phantom odometry, and every
goal will fail in a confusing way until it is fixed.

The 90-second version, which is what you should actually trust:

```bash
python3 - <<'EOF'
import rclpy, math, time, tf2_ros
from rclpy.node import Node
rclpy.init(); n=Node('drift'); b=tf2_ros.Buffer(); tf2_ros.TransformListener(b,n)
t0=time.time(); first=last=None
while time.time()-t0 < 90:
    rclpy.spin_once(n, timeout_sec=0.2)
    try: t=b.lookup_transform('odom','base_link',rclpy.time.Time()).transform.translation
    except Exception: continue
    if first is None: first=(t.x,t.y)
    last=(t.x,t.y)
if first is None: print("no odom -> base_link transform in 90 s - nothing is publishing it")
else: print(f"moved {math.hypot(last[0]-first[0], last[1]-first[1]):.3f} m while parked")
EOF
```

`0.000 m` is the pass. This test read **10.350 m** before the 2026-09-02 fixes.

**VIO can actually see.** Point the camera at a textured scene — a blank wall
or the ceiling is not enough. `/vio/odometry_raw` carries what rtabmap
computed; `/vio/odometry` carries what survived `vio_gate`. If the gate is
dropping nearly everything, the *Log* tab says so — the message text is
`gate: ...`, from the `vio_gate` node:

```
gate: 93/105 dropped, 12 zero-velocity held
```

That is correct behaviour when the camera sees nothing, but it means
`ekf_local` has **no linear-velocity source at all**. The rover will command
forward motion and never register progress. Fix the scene, not the gate.

---

## 2. Teleop first, always

Before any autonomous goal, drive it manually from the Teleop panel. This
proves the whole chain below Nav2 — `/cmd_vel` -> `motor_bridge` -> serial ->
Pico -> motors — and it proves the direction conventions.

- Forward should go forward.
- Positive turn (left) should turn left.

If teleop works and goals do not, the fault is in Nav2 or localization, not
wiring. That single split saves a lot of time.

**Teleop is also the stop button.** `teleop_mux` cancels the running Nav2 goal
on first real input, so nudging a teleop *arrow* aborts an autonomous run. It
is not an e-stop in the safety sense — there is no hardware cut in this stack —
but it is the fastest software stop you have. The panel's STOP button is not
that: it publishes a zero direction, which sits below the mux's 0.02 deadband
and therefore cancels nothing.

**That cuts the other way when you are measuring.** `teleop_mux` publishes on
`/cmd_vel`, so anyone touching the Foxglove teleop panel silently
contaminates any test that reads it — and it cancels the goal you were
watching at the same time. `ros2 topic info /cmd_vel -v` legitimately shows
six publishers here: `teleop_mux`, the velocity smoother, and several
`behavior_server` behaviours. `/cmd_vel_nav` is the clean signal; only
`controller_server` publishes there.

---

## 3. Sending the goal

In the 3D panel, use the **click-to-publish pose** tool. The layout publishes
`geometry_msgs/PoseStamped` on `/athena/goal_click`; `goal_manager` converts it into
`map` at click time and sends the goal (a click sent straight to `/goal_pose` in
`odom` or `base_link` expires after about 10 s). Click the position, drag to set
the final heading, release. Why a goal ended: the *Nav status* line in the *Goal* tab.

**Check the frame the first time.** Foxglove stamps the pose with the panel's
**display frame** (the *Follow* setting). The layout ships with Follow = `odom`,
so a click 2 m ahead of the rover is genuinely 2 m ahead. Open the *Goal pose*
readout tab and confirm:

```
header:
  frame_id: "odom"
```

This matters more than it sounds. If Follow is `map` and `map -> odom` carries
a yaw offset, a goal you *meant* as "2 m forward" is aimed somewhere else
entirely, the planner produces a perfectly correct path to the wrong place, and
the rover turns before driving. That is not a controller bug; the goal was
never where you thought.

Check `map -> odom` yaw whenever you are unsure:

```bash
ros2 run tf2_ros tf2_echo map odom
```

Near-zero yaw is healthy for the current configuration. If you see something
like +89°, `ekf_global` is fusing absolute yaw from a compass — see §6.

---

## 4. Reading what happened

Four places, in the order worth checking.

**Nav feedback tab** (`/navigate_to_pose/_action/feedback`) — is Nav2 even
running the goal? `distance_remaining` should fall. `number_of_recoveries`
climbing means it is stuck and cycling recovery behaviours.

**Speed tab** — the diagnostic plot. Five traces:

| Trace | Topic | Means |
|---|---|---|
| `controller linear m/s` | `/cmd_vel_nav.linear.x` | what the controller wants |
| `controller ANGULAR rad/s` | `/cmd_vel_nav.angular.z` | what the controller wants |
| `commanded m/s` | `/cmd_vel.linear.x` | what actually reached the motor bridge |
| `measured m/s` | `/odometry/local.twist.twist.linear.x` | what the EKF believes happened |
| `measured rad/s` | `/odometry/local.twist.twist.angular.z` | what the EKF believes happened |

`cmd_vel_nav` is the controller's raw output, **before** the velocity smoother.
That distinction is the whole point: it separates "Nav2 is asking for the wrong
thing" from "Nav2 is asking correctly and the request is not reaching the
wheels."

Reading the three levels together is what localises a fault. `cmd_vel_nav`
non-zero with `commanded` flat means the smoother or the mux is eating it.
Both non-zero with `measured` flat means the request reached the bridge and
the rover did not move, or moved and was not seen. And `commanded` non-zero
while `cmd_vel_nav` is flat means someone is driving from the teleop panel.

The signature to watch for:

> **angular saturating while linear sits at exactly 0.00, indefinitely.**

That is `RegulatedPurePursuit` in rotate-to-heading, refusing to translate
until it is pointed at the carrot. It is correct behaviour for a real heading
error, and a bug symptom when the heading error is not real — when it is
phantom odometry, or a lookahead so short that ordinary position noise trips
`rotate_to_heading_min_angle` (0.5 rad).

The lookahead half of that was fixed on 2026-09-04. With velocity scaling
on, the carrot is `clamp(|speed.linear.x| * lookahead_time, min, max)` and
speed is zero at the instant every goal starts, so it pinned at
`min_lookahead_dist` — 0.4 m at the time, which is *inside* a rover whose
footprint reaches x = +0.65. NavFn's 0.1 m grid snap alone was then enough
to put the carrot at −0.58 rad and zero `linear.x`, and it could never
recover, because building speed was the thing that would have lengthened the
lookahead. Measured down a clear corridor with a 2 m goal:

```
velocity-scaled, 0.4 m carrot : linear.x = 0.000 on 160/160 cycles
fixed 1.0 m carrot            : linear.x = 0.350 on 178/178 cycles
```

So `use_velocity_scaled_lookahead_dist` is now `false` with a fixed
`lookahead_dist: 1.0`. If the symptom comes back, check that it is still
false before looking anywhere else.

**Log tab** (`/rosout`) — planner failures, `vio_gate` drop counts, recovery
announcements, costmap warnings. Filter on `WARN`.

**3D panel** — the orange `/plan` line is what the planner produced. If the
orange line is sensible and the rover does not follow it, the problem is the
controller or odometry, not planning. If the orange line itself is wrong, the
goal or the costmap is wrong. This one visual split tells you which half of
the stack to investigate.

---

## 5. Failure modes and what they look like

| What you see | Where to look | Likely cause |
|---|---|---|
| Rover rotates forever, never translates | Speed tab: angular high, linear 0.00 | Phantom odometry (run the parked-drift test in §1), or a lookahead shorter than the footprint — check `use_velocity_scaled_lookahead_dist` is still `false`, see §4 |
| Plan is correct, rover drives somewhere else | *Goal pose* tab | Goal stamped in a frame with a yaw offset |
| Goal instantly reports success | *Nav feedback*, `/gps/fix` | No GPS fix, `/fromLL` returned map (0,0). `goal_manager` guards this; a raw `/goal_pose` click does not |
| Rover commands motion, never registers progress | *Speed* tab: commanded non-zero, measured flat 0 | VIO blind — camera on a blank surface. `ekf_local` has no linear-velocity source |
| Obstacles slide with the rover in 3D | Set Follow to `odom` | Odometry not tracking |
| Nothing marked in the costmap | 3D depth cloud layer | Camera height/pitch wrong in the URDF, or cloud not arriving |
| `number_of_recoveries` climbing | *Log* tab | Stuck; read which behaviour fired |
| Nothing moves, teleop or goal, and no errors | `fuser -v /dev/ttyACM*`, *Log* tab | Something else holds the Pico's port, or `motor_bridge` logged `FIRMWARE NOT RESPONDING` and is streaming into a dead link |
| One wheel does not turn | — | Always hardware. The bridge sends one PWM per side and the firmware writes it to all three motors on that side, so no software path can single a wheel out |
| Connection refused instantly, HTTP 400 | — | Foxglove too old for `foxglove.sdk.v1`. See [docs/FOXGLOVE_PANEL.md](docs/FOXGLOVE_PANEL.md#setup) |
| Empty node/topic list over ssh | `echo $ROS_DOMAIN_ID` | Non-interactive shell, domain 0 instead of 42. See §0 |

---

## 6. Known limitations right now

Read this before trusting a result.

- **`max_wheel_speed` is an unmeasured estimate (0.7 m/s), and so is
  `max_pwm` (255).** `~/.config/athena_drive/params.yaml` holds only
  `min_pwm: 20` and `track_width: 0.85`, so `motor_bridge` falls back to the
  built-in estimate for the other two. `max_wheel_speed` scales every
  velocity Nav2 commands, so distance-to-goal behaviour is only as good as
  that guess.

  Measuring it is two steps, not one. `ros2 run athena_drive calibrate_speed
  --ros-args -p mode:=topspeed` drives the rover and prints the number, but
  **saves nothing** — either run `ros2 run athena_drive calibrate --ros-args
  -p stages:=4`, which asks for the measured distance and writes the file,
  or add the line to `params.yaml` by hand. `motor_bridge` names the
  offenders at startup — `UNCALIBRATED, using built-in estimates for:
  max_wheel_speed, max_pwm` — so check the launch log rather than the file.

- **Absolute heading is not available.** `ekf_global` no longer fuses absolute
  yaw, because the Pixhawk's attitude reads roll −22° / pitch −15° with the
  rover flat. `map` yaw is now dead-reckoned, which is right for local goals
  and **not** sufficient for GPS waypoints. Heading needs to come back from a
  calibrated compass or dual-antenna RTK before waypoint work.
  `navsat_transform.use_odometry_yaw` is still `false` and still reads
  `/imu/data` yaw for the datum — fix both together.

- **Goals beyond ~50 m cannot be planned.** The global costmap is
  `rolling_window: true` at 100 x 100 m, so anything outside ±50 m of the
  rover is off the map. It was 60 x 60 m, which capped legs at ~30 m; at
  0.1 m resolution the larger map is 1e6 cells, about 1 MB, which is nothing
  on this Jetson.

- **A wedged RealSense now invalidates observations rather than going
  unnoticed.** Both costmaps set `expected_update_rate: 2.0` on the depth
  cloud source, so a camera that stops publishing for two seconds gets
  flagged instead of leaving stale obstacles marked forever. It is still
  worth watching the depth cloud in the 3D panel: the costmap has no time
  decay, so anything marked while the camera was healthy stays marked until
  something clears it.

- **Small turns may not move the rover outdoors.** `min_pwm: 20` was measured
  driving *straight*. Skid-steer scrub needs more torque, so corrections at
  ω ≤ 0.2 rad/s (PWM 27–49) may stall on grass or gravel while working fine
  on a hard floor.

- **The rover is blind behind and to the sides.** One forward-facing camera,
  87° wide, nothing rearward. This is why the stack runs its own behaviour
  tree, `behavior_trees/athena_nav_to_pose.xml`: the stock Nav2 tree's
  `Spin` (1.57 rad through 273° it cannot see) and `BackUp` (0.30 m
  reversing a 1.3 m rover into space no sensor has ever observed) are both
  removed. What is left is clear-the-costmaps and wait. Both plugins are
  still loaded by `behavior_server`, so a direct action call can still fire
  them — the tree just never does.

  The practical consequence when reading `number_of_recoveries`: a stuck
  goal now cycles clearing and waiting, and then fails cleanly and hands
  control back, instead of blindly reversing.

---

## 7. Bench testing without moving the rover

```bash
ros2 launch athena_gps_nav bringup.launch.py dry_run:=true
```

`dry_run` logs motor commands instead of sending them. Every panel behaves
normally and you can watch `cmd_vel_nav` respond to a goal. It also leaves
the Pico's serial port free, so `wiring_check` or `calibrate` can run in
another terminal at the same time.

Indoors, add `local_only:=true`. That drops `ekf_global` and
`navsat_transform` and pins `map` to `odom`, which is the right shape for
testing local obstacle avoidance with no sky. `/odometry/global` never
publishes in that mode, so bringup also switches the operator trail to
`/odometry/local` for you — the cyan trail keeps working. That only happens
when bringup starts the panel: a standalone
`ros2 launch athena_remote foxglove.launch.py` still defaults to
`/odometry/global` and needs `trajectory_source:=/odometry/local` passed by
hand.

One caveat that looks exactly like a bug: with `dry_run` a goal needing an
initial turn produces **pure rotation, linear.x pinned at 0.00, forever**. The
rover cannot physically turn, so the heading error never closes and the
controller keeps asking. That is correct. Only judge forward driving with
`dry_run` off.

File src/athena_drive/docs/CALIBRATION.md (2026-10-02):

# Calibration and motor tests

`ros2 run athena_drive calibrate` is the one tool for testing motors and
saving what it measures. Run it once per hardware change, not per drive.
Wheels off the ground for everything except stage 4. Stop the stack first (the
Pico's serial port is exclusive). Back to the [package README](../README.md).

## The menu

`calibrate` opens a menu. Keys also work in `-p stages:=...`, which skips the menu:

| Key | Does |
|---|---|
| `m` | **Manual motor test**: pick one or more motors, a direction, confirm; only that runs. Then repeat, reverse or pick again |
| `d` | Stage 1 direction check, only for the motors you pick |
| `w` | **Wiring map**: Pico GPIO and header pin to motor driver channel (the [pin map](../README.md#pico-to-motor-driver-pin-map)) |
| `s` | Board status and invert flags, read from the Pico |
| `1`-`5` | The five stages below, each on its own |
| `a` | Stages 1-5 in order |
| `q` | Quit |

```bash
ros2 run athena_drive calibrate                                    # menu
ros2 run athena_drive calibrate --ros-args -p stages:=m            # straight to the manual test
ros2 run athena_drive calibrate --ros-args -p stages:=3,4          # these stages, no menu
ros2 run athena_drive calibrate --ros-args -p stages:=all          # stages 1-5
```

Other parameters: `test_pwm` (default 120, the PWM used by the tests), `port`
(default: auto-detect the Pico), `baud` (115200).

**When results are saved.** In the menu, as soon as each stage finishes. With
`stages:=...`, once when the whole run ends (Ctrl-C mid-run saves nothing).

### `m`: manual motor test

- Pick motors by number (`3`, `1,4`), name (`fl ml rl fr mr rr`) or `left` / `right` / `all`.
- Direction is `f` or `b`, with an optional PWM (`f 150`).
- It prints the plan, including each motor's PWM and DIR wires, and asks to
  confirm. Each run auto-stops after ~1.5 s. After a run: Enter repeats, `r`
  reverses, `n` picks new motors, `q` returns to the menu.
- Several motors run **together** through the firmware's `G <mask> <pwm>`
  command (bit 0 = motor 1). `G` is compiled in the current firmware source
  but **not yet flashed to the Pico**. `calibrate` asks the board (via its help
  text) and, if it has no `G`, runs the chosen motors one after another and says
  so before you confirm. Reflash `athena_drive_fw` to run them together
  ([FIRMWARE.md](FIRMWARE.md#flashing)).

## The five stages

| Stage | Does | Saved to |
|---|---|---|
| 1 motor directions | runs each motor forward **then reverse**, ~1.5 s each; you answer what the wheel did | **Pico flash** (invert flags) |
| 2 side check | spins left; "counter-clockwise from above?" | nothing; tells you the fix |
| 3 PWM deadband | steps PWM 10, 20 ... 140, asks "did all six turn?", stops at the first yes | `min_pwm` in the config file |
| 4 top speed | **drives on the floor** at full PWM for N s (default 3); you enter the measured distance | `max_wheel_speed` |
| 5 track width | you enter the distance between left and right wheel centre lines | `track_width` |

Stage 4 needs clear floor and a mark at the front edge. The ~0.3 s firmware
ramp makes short runs read a little low. Stage 2 failure fix: swap the left
and right driver connections, **or** flip all six invert flags (`I 1 1` ...
`I 6 1`), never both; then redo stage 1.

### Stage 1 verdicts

Both directions are tested and each motor is classified from the two answers:

| "rolled forward?" | "rolled backward?" | Verdict | What happens |
|---|---|---|---|
| yes | yes | ok | next motor |
| no | no, but it did move | flipped | invert flag toggled on the Pico, saved, motor re-tested |
| no | no, and it never moved | **dead** | power, motor leads or driver channel |
| exactly one yes | | **stuck** | ran the same way both times: DIR line or H-bridge fault |

Only `flipped` is fixable by calibration. The firmware applies invert as
`spwm = -spwm`, a symmetric sign flip: it can make a motor run the wrong way
in both directions but never the same way in both. So `stuck` is reported as
a hardware fault, not handed a flag that cannot help. Faults are repeated in a
block at the end so they do not scroll past. Stage 1 starts from the board's real
flags, so a motor already flipped toggles back rather than being re-sent the
same value. A motor that cannot reverse passes a forward-only test and then
fails the moment Nav2 asks for a turn, which is why both directions are tested.

## Where the settings live

| What | Where | Why |
|---|---|---|
| Motor directions (invert flags) | **the Pico's flash** | Direction is a property of the wiring, so it belongs to the board: swap the Jetson, reinstall ROS, and the motors still spin the right way. It must be there anyway: the bridge sends one PWM value per *side*, so it cannot flip a single wheel |
| `min_pwm`, `max_wheel_speed`, `track_width` | `~/.config/athena_drive/params.yaml` | Loaded by `motor_bridge` at startup, so calibrated values apply to every launch with no arguments. Outside the package so a rebuild cannot wipe it |

Precedence: **explicit argument > saved calibration > built-in estimate**, so
a one-off experiment never silently becomes permanent:

```bash
ros2 launch athena_drive drive.launch.py max_pwm:=120    # cautious, this run only
```

## What is in the file today

```yaml
min_pwm: 20
track_width: 0.85
```

`max_wheel_speed` and `max_pwm` are absent, so the rover runs on the built-in
estimates of **0.7 m/s and 255**. `max_wheel_speed` scales every velocity Nav2
commands, so commanded speeds and distances are only as good as that guess:
run stage 4 on the floor (`calibrate --ros-args -p stages:=4`). A sanity check
on 0.7 m/s: wheels about 20 cm across give 0.628 m of circumference, so about
67 wheel RPM. `max_pwm` has no measuring tool; 255 is the default, lower it
only deliberately.

`motor_bridge` warns per missing key at startup (it reports each key
separately, so an incomplete file does not look calibrated):

```
loaded calibration from /home/robo/.config/athena_drive/params.yaml: {'min_pwm': 20, 'track_width': 0.85}
motor_bridge up: track=0.85 m, max_wheel_speed=0.7 m/s, pwm=[20,255]
[WARN] UNCALIBRATED, using built-in estimates for: max_wheel_speed, max_pwm. ...
```

No `UNCALIBRATED` line means all four values are either saved or passed
explicitly. A `max_wheel_speed` of exactly `0.7` is the fallback, not a measurement.

## Single-purpose tools

`calibrate` covers all of this. These re-check one thing without the wizard:

```bash
ros2 run athena_drive wiring_check                           # each motor forward in turn
ros2 run athena_drive wiring_check --ros-args -p mode:=sides # left side, then right side
ros2 run athena_drive wiring_check --ros-args -p mode:=spin  # forward, then spin left
ros2 run athena_drive calibrate_speed --ros-args -p mode:=deadband
ros2 run athena_drive calibrate_speed --ros-args -p mode:=topspeed -p seconds:=3.0
```

- `wiring_check` options: `-p motor:=3` (one motor), `-p pwm:=150` (default
  120), `-p pause:=5.0` (default 3 s between motors). It runs on a schedule and
  reads no answers; `calibrate` is the interactive one. See
  [TESTING.md](TESTING.md#1-each-motor-turns-the-right-way) for what to look for.
- `calibrate_speed` `deadband` sweeps PWM 10 to 120 in tens, wheels off the
  ground. `topspeed` **drives the rover on the floor** at full PWM (`-p pwm:=`
  to change) for `seconds`, then tells you to divide your measured distance by
  the time.
- These print results and **do not save them**. Only `calibrate` writes
  `params.yaml`. Either use `calibrate`, or hand-edit the file (the bridge reads
  it at the next launch):

```yaml
min_pwm: 20
track_width: 0.85
max_wheel_speed: 0.62      # add the number you measured
```

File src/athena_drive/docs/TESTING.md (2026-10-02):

# Testing the drive end to end

Checks, in order, from bare wheels to Nav2 driving around an obstacle. Prop
the rover up so the wheels spin free for every step except where noted, and
stop the stack before using `wiring_check` or `calibrate` (the Pico's serial
port is exclusive). Back to the [package README](../README.md).

Everything downstream assumes ROS conventions (REP-103) in the robot's frame:
**+x forward, +y left, +z up, and +yaw is counter-clockwise seen from above.**

## 1. Each motor turns the right way

```bash
ros2 run athena_drive wiring_check          # wheels off the ground
```

It drives motors 1 to 6 forward one at a time, naming each. For every one: **does
the top of that wheel roll toward the front of the rover?**

- Wrong direction on one wheel: flip that motor's invert flag (`I <n> 1`, or let
  `calibrate` do it), **or** swap its two power leads at the driver. One, not both.
- **No movement on one wheel: hardware.** The bridge sends one PWM per side and
  the firmware writes it to all three motors on that side, so no software path
  can single one wheel out. Check power, leads, driver channel (the
  [pin map](../README.md#pico-to-motor-driver-pin-map) says which wires).
- Wrong on all three of a side: set `invert_left` or `invert_right` on
  `motor_bridge`. Fix it in the wiring **or** in software, never both.

Options: `-p motor:=3` (one motor), `-p pwm:=150` (stiff gearbox), `-p pause:=5.0`.
`-p mode:=sides` drives the whole left side, then the right, with `V`; all three
wheels on the active side should turn together. If **one** wheel of a side stays
still while the other two turn, that is never software.

## 2. The sides are not swapped

```bash
ros2 run athena_drive wiring_check --ros-args -p mode:=spin
```

Drives forward, then spins left. **Spin left must rotate counter-clockwise seen
from above.** If it spins the other way the left and right driver connections
are exchanged.

## 3. It matches what ROS believes

With the nav stack running, drive and watch `/odometry/local`:

```bash
ros2 topic echo /odometry/local --field pose.pose.position
ros2 run tf2_ros tf2_echo odom base_link          # roll/pitch/yaw, live
```

- Drive **forward**: `x` increases.
- Spin **left**: yaw increases. `/imu/data` carries a quaternion, not an angle,
  so read yaw off TF as above.

Whole-system check, which catches what the above missed:

```bash
ros2 run athena_gps_nav tf_check
```

It verifies gravity points **+z** in `base_link` (catches an upside-down or
unconverted IMU; a wrong IMU still reads 9.81, only the *sign* gives it away) and
that the depth cloud lands at **+x** (catches a camera rotated sideways).

In RViz, Fixed Frame `odom`, drive forward a metre: the robot marker moves along
its own +x and obstacles stay **fixed in the world**. If obstacles slide along
with the robot, odometry is not tracking the motion.

## 4. Bring-up in three stages

Each stage proves one thing before the next depends on it.

**Stage 1, teleop only** (no localization involved):

```bash
ros2 launch athena_drive drive.launch.py
ros2 run athena_drive teleop
```

Arrows drive, releasing them stops the rover. Verify: forward goes forward and
left goes left; releasing the keys stops it within ~0.4 s; unplugging the Pico USB
stops it (the firmware watchdog).

**Stage 2, Nav2 with GPS.** Stop the stage 1 launch first: bringup includes
`drive.launch.py`, and a second `motor_bridge` cannot open the port, so it streams
into nothing while the first one drives.

```bash
ros2 launch athena_gps_nav bringup.launch.py
ros2 run athena_gps_nav stack_check                 # every line PASS
```

In RViz (`rviz2 -d ~/athena/src/athena_gps_nav/config/athena_bench.rviz`, Fixed
Frame `odom`) use **2D Goal Pose** a few metres ahead. Watch for a path on
`/plan`, `/cmd_vel` publishing and the rover following. Before trusting a goal,
drive forward a metre by hand and confirm `x` increases in `/odometry/local`;
if the rover drives forward while odometry says backwards, a goal drives it away
from the target.

Watch `/cmd_vel_nav`, not `/cmd_vel`, to see what the *controller* asked for.
`/cmd_vel` has six publishers (`teleop_mux`, the velocity smoother and several
`behavior_server` behaviours), so Foxglove teleop contaminates a reading taken
there. Only `controller_server` publishes `/cmd_vel_nav`;
`ros2 topic info /cmd_vel -v` lists the rest.

Outdoors, with sky, record and follow a GPS route:

```bash
ros2 run athena_gps_nav gps_waypoint_logger --ros-args -p output_file:=/home/robo/route.yaml
ros2 run athena_gps_nav gps_waypoint_follower --ros-args -p waypoints_file:=/home/robo/route.yaml
```

Expect arrival within a few metres, not centimetres: GPS here is **+-3.5 m
1-sigma**, a receiver limit, not a tuning one.

**Stage 3, local obstacle avoidance.** This is the depth camera's job and works
with **no GPS at all** (the local costmap lives in `odom`).

- *Static:* put a box ~1.5 m ahead, slightly off the line to a goal and send the
  goal. The path should bend around the box. RViz shows dark lethal cells where
  the box is, with a lighter inflation halo (the clearance Nav2 keeps).
- *Dynamic:* with the rover driving, step into its path a few metres ahead. It
  should re-plan around you and cells behind you should clear. Stand still directly
  in front: it should stop, not push through.
- *If it does not stop:* `ros2 topic hz /camera/camera/depth/color/points_downsampled`
  (camera alive?) and `ros2 run athena_gps_nav stack_check`. `local costmap
  marking` at 0 cells means the camera is not reaching the costmap: a perception
  fault, not a controller one.

Blind spots: the D435i sees nothing closer than ~0.2 m, nothing outside its ~87
degree cone and nothing behind. The costmap remembers what it saw, but a rover
turning in place only clears what the camera sees now. Approach obstacles head-on.

## Recommended order for the first real drive

1. `max_pwm:=100`: deliberately slow while you build confidence. It is an argument
   of `drive.launch.py`; `bringup.launch.py` does not forward it, so for the Nav2
   steps temporarily add `max_pwm: 100` to `~/.config/athena_drive/params.yaml`
   (and remove it after)
2. Teleop in open space
3. Teleop near an obstacle, watching the costmap
4. A short Nav2 goal, ~2 m, clear ground
5. A Nav2 goal with one obstacle in the way
6. GPS waypoints outdoors

Keep a hand near the Pico's USB cable throughout; pulling it is the fastest
stop you have.

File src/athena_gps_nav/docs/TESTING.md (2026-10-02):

# Checking that it works

Eyeballing tells you *whether* something is wrong; the automated checks tell
you *how much*. Back to the [package README](../README.md).

1. [Health check](#health-check): `stack_check`, every link PASS/FAIL
2. [RViz](#rviz): what to look at
3. [Camera mount](#camera-mount): `mount_check.py`
4. [Hands-on tests](#hands-on-tests): no motors needed
5. [Measurements](#measurements): drift, costmap sliding, TF orientation, no-hardware bench

## Health check

```bash
ros2 run athena_gps_nav stack_check                      # 10 s window
ros2 run athena_gps_nav stack_check --ros-args -p window:=30.0
```

It counts messages for the window, prints one block per stage plus `TF TREE`
and `NAV2` sections and a closing `ALL CHECKS PASS` or `n FAIL`, then exits on
its own (nothing to Ctrl-C). Extract from a healthy indoor run:

```
SENSORS
  [PASS]  pixhawk imu                 48.5 Hz
  [PASS]  imu physics (at rest)      |g|=9.81 m/s2, attitude-vs-accel residual 0.002, tilt r=+0 p=+0 deg
  [PASS]  pixhawk gps                  5.2 Hz, NO FIX (indoors?)
  [PASS]  depth cloud (camera)         6.6 Hz

OBSTACLE PERCEPTION  (depth camera -> costmap)
  [PASS]  downsampled cloud            6.6 Hz, 4812 pts/frame
  [PASS]  local costmap marking      767 lethal + 888 inflated cells
  [PASS]  global costmap marking     731 lethal + 902 inflated cells

ODOMETRY / LOCALIZATION
  [PASS]  VIO raw (rtabmap)           11.4 Hz
  [PASS]  VIO gated                   11.2 Hz (2 implausible dropped)
  [PASS]  EKF local (odom)            29.8 Hz
  [PASS]  EKF global (map)            27.3 Hz
  [FAIL]  navsat gps->map              0.0 Hz  (needs a GPS fix)
```

Expected, not bugs:

- `navsat gps->map` FAILs without a satellite fix (indoors, or the GPS problem in
  [TROUBLESHOOTING.md](TROUBLESHOOTING.md#gps-has-no-fix)). `navsat_transform`
  also waits `delay: 45.0` s before latching a datum, so re-run after a minute
  outdoors before believing that line. Obstacle avoidance depends on neither.
- With `local_only:=true`, `EKF global (map)` and `navsat gps->map` both FAIL: those
  nodes are deliberately not running.
- `NAV2 / cmd_vel` reads `0.0 Hz (idle - no goal sent)` and is never a FAIL.
- `imu physics (at rest)` compares the accelerometer against the FMU's own
  attitude quaternion, which is known bad on this FMU (flat, it decodes to roll
  -22.3 / pitch -15.4 degrees). A large attitude-vs-accel residual here is that
  known fault, not new damage; nothing fuses that attitude. `tf_check`'s gravity
  checks are the ones to trust (they use the URDF transform).
- Rate floors are set well below what the hardware achieves, so PASS means
  "alive", not "fast": IMU > 30 Hz, GPS > 1, depth > 3, downsampled cloud > 1,
  VIO > 2, EKFs > 15 Hz (healthy is 19-26, a lost Pixhawk IMU drops them to 7-8),
  navsat > 1.

## RViz

```bash
rviz2 -d ~/athena/src/athena_gps_nav/config/athena_bench.rviz
```

Run it on a **laptop** if you can (on the Jetson itself, directly or over `ssh -X`, it eats a whole CPU core and
roughly halves visual odometry, ~10 Hz to ~5 Hz). That needs `ROS_DOMAIN_ID=42` in
every shell on both ends and a network path that carries DDS; on campus WiFi it
usually does not, so use the setup in
[athena_remote Option C](../../athena_remote/README.md#option-c-native-ros-on-a-laptop)
or use Foxglove. The `.rviz` file is on the Jetson, so `scp` it to the laptop
first (the `athena_remote` guide has the command); plain `rviz2` with no `-d`
works if you add the displays by hand.

**Set Fixed Frame first** (Global Options): it decides what you are testing.

| Fixed frame | Tests |
|---|---|
| `odom` | camera and IMU only; GPS cannot affect anything you see. **Use this indoors and for everything below** |
| `map` | GPS too. Meaningful only with a fix; indoors it wanders metres with multipath, which is the GPS, not a bug |
| `base_link` | the rover's own view, with the world moving around it |

Displays (the `.rviz` file has them; add by hand otherwise):

| Display | Topic | Should look like |
|---|---|---|
| RobotModel | `/robot_description` | the rover, nose block forward |
| Local Costmap (Map) | `/local_costmap/costmap` | dark cells where obstacles are, lighter halo around them |
| Depth Cloud (PointCloud2) | `/camera/camera/depth/color/points_downsampled` | 3D points sitting exactly on those cells |
| Odometry local (green) | `/odometry/local` | an arrow that stays put when the rover does |
| Odometry global (orange) | `/odometry/global` | same, but drifts with GPS indoors; nothing publishes it under `local_only` |
| Path | `/plan`, `/athena/trajectory` | a line to your goal once you set one; the driven trail |
| MarkerArray | `/athena/waypoints` | saved places |
| TF | `/tf`, `/tf_static` | one connected tree, no floating frames |

A second Map display on `/global_costmap/costmap` comes up blank and fills in as
the rover moves: it is 100 x 100 m with `always_send_full_costmap: False`, so it
publishes incremental updates (a full 1e6-cell republish at 1 Hz is ~1 MB/s down
the SSH tunnel). The local costmap keeps `True`; it is only 160 x 160 cells.

Frames the URDF publishes under `base_link`: `base_footprint`, `camera_link`,
`imu_link`, `gps_link`, `nose_marker` and six `wheel_*` links (twelve links with
`base_link`), plus `camera_camera_link` bridged from the RealSense driver by a
static transform in `sensors.launch.py`. There are no mast frames: `camera_mast`
and `gps_mast` were deleted on 2026-09-03, so seeing either name in a config or
script means it is stale.
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

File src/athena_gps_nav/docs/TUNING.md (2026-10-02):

# Tuning

Parameter by parameter: what each is now, and why. Costmap and controller
values are in `config/nav2_params.yaml`, filter values in
`config/dual_ekf_navsat.yaml`; with `--symlink-install`, editing either takes
effect on the next relaunch. Back to the [package README](../README.md). For
the design reasoning see [../ARCHITECTURE.md](../ARCHITECTURE.md).

Symptom first? Jump to [Symptom table](#symptom-table).

## Obstacle detection

Both costmaps carry the same obstacle layer, `stvl_layer`
(spatio_temporal_voxel_layer), reading the one cloud twice: `realsense_mark`
marks, `realsense_clear` clears by view frustum. Inflation differs.

Under `stvl_layer` -> `realsense_mark`, identical in both:

| Parameter | Now | What it does |
|---|---|---|
| `topic` | `/camera/camera/depth/color/points_downsampled` | the cloud both costmaps consume (not the raw one) |
| `filter` | `passthrough` | **required**: STVL applies the two height limits only inside this filter. With `""` the floor is marked lethal everywhere |
| `obstacle_range` | 3.0 m | how far obstacles get marked |
| `min_obstacle_height` | 0.10 m | below this counts as ground. Measured in the **costmap** frame where `base_link` is z = 0, so 0.10 is 0.20 m above the actual ground. It is not a camera height; setting it from one is how the floor ends up marked |
| `max_obstacle_height` | 1.8 m | higher is ignored (doorframes, branches) |
| `expected_update_rate` | 2.0 s | if no cloud arrives for this long the costmap reports itself not-current and the controller stops. Unset (0.0) means never checked: a wedged camera would leave stale obstacles frozen with no warning |

Under `stvl_layer` -> `realsense_clear`, identical in both. A voxel inside
this frustum that no new point re-marks is removed, whatever is behind it:
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

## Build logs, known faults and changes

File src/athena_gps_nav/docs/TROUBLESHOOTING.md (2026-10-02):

# Troubleshooting and known limitations

Start with `ros2 run athena_gps_nav stack_check` (see
[TESTING.md](TESTING.md#health-check)); it names the broken link. Tuning
symptoms (overshoot, yawing in place, smeared obstacles) are in
[TUNING.md](TUNING.md#symptom-table). Back to the [package README](../README.md).

| Symptom | Go to |
|---|---|
| `ros2 topic list` is empty from a non-interactive shell | the shell is on domain 0: `export ROS_DOMAIN_ID=42` ([why](../../athena_remote/README.md#option-b-ros-cli-over-ssh)) |
| IMU rate low, MAVLink errors, `link corruption` above a few percent | [Pixhawk link](#check-the-pixhawk-link-before-blaming-gps-or-imu) |
| Pixhawk missing, or disconnects | [Pixhawk missing or silent](#pixhawk-missing-or-silent) |
| `fix_type=0`, no satellites | [GPS has no fix](#gps-has-no-fix) |
| Both costmaps empty, everything else healthy | [Costmap is empty](#costmap-is-empty) |
| `Frames didn't arrived within 5 seconds` | [Camera stalls silently](#camera-stalls-silently) |
| `std::bad_array_new_length` from rtabmap | [rtabmap crashes instantly](#rtabmap-crashes-instantly) |
| Rover turns exactly 90 degrees left | the stock behaviour tree is in use ([TUNING.md](TUNING.md#recovery-behaviour)); or a phantom obstacle, check with `mount_check.py costmap` |
| `/cmd_vel` publishes but wheels do not turn | the Pico's serial port is held by another process, or the Pico is not answering: [athena_drive README](../../athena_drive/README.md#safety) |

## Check the Pixhawk link before blaming GPS or IMU

`pixhawk_bridge` prints this every 10 s:

```
imu msgs: 489 ..., gps msgs: 50 (fix_type=3, sats=11), link corruption: 0.0%
```

Anything above a few percent means the serial link is overrunning and **every**
sensor downstream degrades. Measured on this FMU:

| baud | good frames / 18 s | corrupt | usable IMU |
|---|---|---|---|
| 115200 | 91 | **33.1 %** | 11 |
| **921600** | **1082** | **8.0 %** | **129** |

After also silencing streams the node never reads, corruption drops to **0.0 %**.
`baud` therefore defaults to **921600**. The old `athena_slam` nodes used 115200,
which is why they behaved erratically.

## Pixhawk missing or silent

Signature of a failing USB cable seen on this rover:

```
usb 1-2-port1: Cannot enable. Maybe the USB cable is bad?
usb 1-2.1: can't read configurations, error -32
usb 1-2-port1: unable to enumerate USB device
```

```bash
sudo dmesg | grep 'usb 1-2.1'         # disconnect history
lsusb | grep 26ac                     # on the bus?
ls /dev/serial/by-id/ | grep -i px4   # serial node present?
```

Visible in `lsusb` but **no serial node**, or a node with no heartbeat, means the
physical link is failing. Every disconnect reboots the FMU and cold-restarts the
GPS, which is the usual reason a fix never holds. Swap the cable first, then try
another port. Re-binding the parent hub sometimes revives it temporarily:

```bash
sudo sh -c 'echo 1-2 > /sys/bus/usb/drivers/usb/unbind'
sudo sh -c 'echo 1-2 > /sys/bus/usb/drivers/usb/bind'
```

## GPS has no fix

```bash
# stop the stack first: this needs exclusive access to the serial port
ros2 run athena_gps_nav gps_diagnose --seconds 120
```

`gps_diagnose` is **not a ROS node**: it talks to the FMU with pymavlink and
parses its own `argparse` flags (`--seconds`, `--port`, `--baud`).
`--ros-args -p seconds:=120` is silently ignored and you get the 30 s default.
It exits 0 on a 3D fix, 1 with no GPS telemetry at all, 2 with telemetry but no
usable fix.

| fix_type | Meaning |
|---|---|
| **0** | "no GPS device": read the caveat below |
| **1** | receiver present, no lock: go outside and wait |
| 2 | 2D only, no altitude |
| **3+** | 3D fix: what `navsat_transform` needs |

**Caveat:** on this PX4 build a receiver that is merely *searching* also reports
`fix_type=0`, `sats=0` and "GPS not present", indistinguishable from an unplugged
module. It once sat like that for over two hours and then acquired normally. **Do
not call it a hardware fault from `fix_type=0` alone**: give it 30+ minutes with
sky view.

**Current state on this rover:** the module powers up and talks to the Pixhawk
cleanly (thousands of messages, zero link corruption) but reports zero satellites
indoors and outdoors. The software path is ruled out; the remaining candidates are
the antenna and the RF path. `/gps/fix` still carries a lat/lon with `status: -1`
and a large covariance, so a position appears on the map that is not a fix.

Already ruled out, no need to retest: pymavlink's 1200-baud probe does **not**
reboot the FMU; heavy telemetry load does **not** starve the GPS task; the bridge is
**not** at fault (MAVROS reports identically; use it as a referee):

```bash
ros2 launch mavros px4.launch \
  fcu_url:=/dev/serial/by-id/usb-3D_Robotics_PX4_FMU_v2.x_0-if00:921600
ros2 topic echo /mavros/global_position/raw/fix --once
```

## Costmap is empty

The RealSense pointcloud filter's parameter namespace is named after the
librealsense processing block, and on this Jetson it is **`pointcloud__neon_`**,
not `pointcloud`. Setting `pointcloud.enable: True` fails **silently**: no cloud,
both costmaps empty, everything else healthy. `sensors.launch.py` sets both names.

```bash
ros2 topic info /camera/camera/depth/color/points   # Publisher count must be 1
ros2 param list /camera/camera | grep -i pointcloud # find the real namespace
```

## Camera stalls silently

Streams stop with `Frames didn't arrived within 5 seconds` despite a healthy USB 3
link. USB autosuspend was the cause; a udev rule now pins `power/control=on`. To
recover:

```bash
sudo sh -c 'echo 2-1.3 > /sys/bus/usb/drivers/usb/unbind'
sudo sh -c 'echo 2-1.3 > /sys/bus/usb/drivers/usb/bind'
```

## rtabmap crashes instantly

`std::bad_array_new_length` on startup means `~/rtab` is being sourced. That
source build has been ABI-broken since the Aug 2026 apt upgrade. Use the apt
package (`ros-humble-rtabmap-odom`) and remove `~/rtab` from `.bashrc`.

## Known limitations

- **GPS absolute accuracy is +-3.5 m 1-sigma, measured**, even at HDOP 0.98: a
  receiver floor, not a tuning one; RTK is the only route to sub-metre. It is
  *absolute* error: goal and robot pose live in the same map frame and wander
  together, so Nav2 still converges on `xy_goal_tolerance: 0.5`; the rover just
  ends up within +-3.5 m of where you meant. If it hunts near a goal, widen the
  tolerance rather than tightening it.
- Indoor GPS wanders tens of metres from multipath; every map-frame view inherits
  that. Only odom-frame behaviour is meaningful indoors.
- Visual odometry needs texture and depth in view; a blank wall at 30 cm resets
  tracking repeatedly. People moving in the camera's view register as robot motion
  (`vio_gate` drops the big spikes; keep the scene still for clean numbers).
- The depth camera has a ~0.2 m minimum range and ~87 degree horizontal field of
  view, and the downsampler also drops returns closer than 0.25 m as self-hits.
  Anything closer, directly behind, or outside that cone is invisible. The costmap
  remembers what it saw, but a rover turning in place only clears what the camera
  sees now.
- **There is no rear-facing sensor.** That is why Spin and BackUp were removed from
  the behaviour tree and a failed goal now stops rather than manoeuvring. Reversing
  this rover is an operator decision.
- Absolute heading is not fused; map yaw is dead-reckoned
  ([TUNING.md](TUNING.md#heading-the-compass-is-not-used)). GPS waypoint work needs a
  real heading source first.
- `gps_link` (0, 0, 0.25) in the URDF is an **assumption**, not a measurement.
  `navsat_transform` uses it to remove the antenna lever arm: harmless for local
  obstacle avoidance, worth a tape measure before waypoint work.
- **RViz on the Jetson costs a full CPU core.** Close it for serious measurements.
- The Pico must run the `V <left> <right>` firmware in
  `athena_drive/firmware/athena_drive_fw`. The `athena_drive` bridge speaks only
  that protocol and has no legacy fallback. The deprecated `drive` package has one
  (`legacy_protocol:=true`) but `bringup` deliberately does not use that package: it
  hardcodes a `/dev/ttyACM*` number that enumerates as the Pixhawk about half the
  time ([drive/README.md](../../drive/README.md)).

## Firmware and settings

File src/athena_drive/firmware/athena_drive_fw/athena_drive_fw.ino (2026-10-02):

/*
 * Athena rover motor controller. Raspberry Pi Pico W
 * 6 wheels, 3 per side, each a DC motor on a DIR + PWM driver channel.
 *
 * ── Serial protocol, 115200 baud, newline-terminated ────────────────
 *   V <left> <right>   variable drive. Signed PWM -255..255 per SIDE,
 *                      positive = that side drives the rover FORWARD.
 *                      e.g. "V 120 -80"   (left fwd 120, right rev 80)
 *   M <n> <pwm>        drive ONE motor only, for wiring checks.
 *                      n: 1=FL 2=ML 3=RL 4=FR 5=MR 6=RR
 *                      e.g. "M 1 120"     (front-left forward)
 *                      Auto-stops after MOTOR_TEST_MS so a mistake
 *                      cannot run away.
 *   G <mask> <pwm>     drive SEVERAL motors at once, same auto-stop as M.
 *                      mask bit 0 = motor 1 ... bit 5 = motor 6,
 *                      e.g. "G 5 120" runs motors 1 and 3 together.
 *   F B L R S         legacy discrete moves at the stored speed / stop
 *   P <0-255>          set the speed F/B/L/R use
 *   ?                  status line
 *   H                  this help
 *
 * ── Why it is built this way ────────────────────────────────────────
 *  20 kHz PWM.  The RP2040 core defaults to ~1 kHz, which sits right in
 *  the audible band (loud whine) and gives poor low-speed torque because
 *  each pulse is long relative to the motor's electrical time constant.
 *  20 kHz is above hearing and lets the winding current stay continuous,
 *  so slow speeds are smooth and controllable instead of steppy.
 *
 *  Slew limiting.  Commanded PWM ramps toward the target rather than
 *  stepping.  Protects the gearboxes, stops the wheels breaking traction
 *  on every command change, and keeps the motion smooth enough that the
 *  visual odometry upstream can actually track it.
 *
 *  Watchdog.  If no valid command arrives for WATCHDOG_MS the motors stop.
 *  The host streams at 20 Hz, so a crashed node, unplugged cable or dead
 *  Jetson halts the rover in under half a second.
 *
 * Pin map and motor polarity are unchanged from the original sketch:
 * left side forward = DIR LOW, right side forward = DIR HIGH.
 */

#include <EEPROM.h>

/* Per-motor direction is stored in flash, not compiled in.
 * A rover gets rewired: one motor's leads get swapped, a driver board is
 * replaced. Recompiling for that is slow and easy to get wrong, so the
 * calibration wizard flips a motor over serial and the setting survives a
 * power cycle. EEPROM here is flash-backed emulation, so it must be
 * commit()ed explicitly. */
#define EEPROM_SIZE   64
#define CONFIG_MAGIC  0xA7

struct Config {
  uint8_t magic;
  uint8_t invert[6];   // 1 = this motor's forward direction is flipped
  uint8_t speedVal;    // speed used by legacy F/B/L/R
};
Config cfg;

// ───────────────────────── pins (unchanged) ─────────────────────────
#define FRONT_M1_PWM  8    // M1 = LEFT side
#define FRONT_M1_DIR  9
#define FRONT_M2_PWM  6    // M2 = RIGHT side
#define FRONT_M2_DIR  7

#define MID_M1_PWM   18
#define MID_M1_DIR   19
#define MID_M2_PWM   20
#define MID_M2_DIR   21

#define REAR_M1_PWM  10
#define REAR_M1_DIR  11
#define REAR_M2_PWM  12
#define REAR_M2_DIR  13

// polarity taken from the original, proven sketch
#define LEFT_FWD_LEVEL   LOW
#define RIGHT_FWD_LEVEL  HIGH

// ───────────────────────── tuning ─────────────────────────
#define PWM_FREQ_HZ      20000   // above audible; smooth at low duty
#define WATCHDOG_MS      500     // stop if the host goes quiet
#define RAMP_INTERVAL_MS 10      // slew update period
#define RAMP_STEP        8       // PWM counts per interval
                                 //   0->255 in ~0.32 s, full reverse ~0.64 s
#define MOTOR_TEST_MS    1500    // "M" command auto-stop

// signed PWM, -255..255, positive = forward
int targetL = 0, targetR = 0;    // what the host asked for
int currentL = 0, currentR = 0;  // what the motors are actually doing

unsigned long lastCmdMs   = 0;
unsigned long lastRampMs  = 0;
unsigned long motorTestMs = 0;   // non-zero while an "M" test is running
bool wdtTripped = false;

char lineBuf[40];
uint8_t lineLen = 0;

struct Motor { uint8_t pwm; uint8_t dir; bool leftSide; };
const Motor MOTORS[6] = {
  {FRONT_M1_PWM, FRONT_M1_DIR, true },   // 1 FL
  {MID_M1_PWM,   MID_M1_DIR,   true },   // 2 ML
  {REAR_M1_PWM,  REAR_M1_DIR,  true },   // 3 RL
  {FRONT_M2_PWM, FRONT_M2_DIR, false},   // 4 FR
  {MID_M2_PWM,   MID_M2_DIR,   false},   // 5 MR
  {REAR_M2_PWM,  REAR_M2_DIR,  false},   // 6 RR
};
const char *MOTOR_NAME[6] = {"front-left", "mid-left", "rear-left",
                             "front-right", "mid-right", "rear-right"};

// ───────────────────────── motor output ─────────────────────────
void driveMotor(const Motor &m, int spwm) {
  int idx = &m - &MOTORS[0];
  if (idx >= 0 && idx < 6 && cfg.invert[idx]) spwm = -spwm;
  int mag = abs(spwm);
  if (mag > 255) mag = 255;
  bool fwd = (spwm >= 0);
  int level = m.leftSide ? (fwd ? LEFT_FWD_LEVEL  : !LEFT_FWD_LEVEL)
                         : (fwd ? RIGHT_FWD_LEVEL : !RIGHT_FWD_LEVEL);
  digitalWrite(m.dir, level);
  analogWrite(m.pwm, mag);
}

void applySide(bool leftSide, int spwm) {
  for (int i = 0; i < 6; i++)
    if (MOTORS[i].leftSide == leftSide) driveMotor(MOTORS[i], spwm);
}

void applyMotors() {
  applySide(true,  currentL);
  applySide(false, currentR);
}

void hardStop() {
  targetL = targetR = 0;
  currentL = currentR = 0;
  motorTestMs = 0;
  applyMotors();
}

// ───────────────────────── config ─────────────────────────
void configDefaults() {
  cfg.magic = CONFIG_MAGIC;
  for (int i = 0; i < 6; i++) cfg.invert[i] = 0;
  cfg.speedVal = 200;
}

void configLoad() {
  EEPROM.begin(EEPROM_SIZE);
  EEPROM.get(0, cfg);
  if (cfg.magic != CONFIG_MAGIC) configDefaults();
  for (int i = 0; i < 6; i++) if (cfg.invert[i] > 1) cfg.invert[i] = 0;
}

void configSave() {
  cfg.magic = CONFIG_MAGIC;
  EEPROM.put(0, cfg);
  if (EEPROM.commit()) Serial.println(F("config saved"));
  else Serial.println(F("ERR config save failed"));
}

void printInvert() {
  Serial.print(F("invert:"));
  for (int i = 0; i < 6; i++) {
    Serial.print(' ');
    Serial.print(i + 1);
    Serial.print('=');
    Serial.print(cfg.invert[i]);
  }
  Serial.println();
}

// ───────────────────────── ramping ─────────────────────────
int stepToward(int current, int target) {
  if (current < target) {
    current += RAMP_STEP;
    if (current > target) current = target;
  } else if (current > target) {
    current -= RAMP_STEP;
    if (current < target) current = target;
  }
  return current;
}

// ───────────────────────── commands ─────────────────────────
void feedWatchdog() {
  lastCmdMs = millis();
  if (wdtTripped) {
    wdtTripped = false;
    Serial.println("WDT cleared");
  }
}

void printHelp() {
  Serial.println(F("athena-drive v2  (6 motors, variable speed)"));
  Serial.println(F("  V <l> <r>    drive, signed PWM -255..255 per side"));
  Serial.println(F("  M <n> <pwm>  ONE motor for wiring checks, n=1..6"));
  Serial.println(F("               1=FL 2=ML 3=RL 4=FR 5=MR 6=RR"));
  Serial.println(F("  G <mask> <pwm>  several motors at once (bit0=motor 1)"));
  Serial.println(F("  F B L R S    legacy moves / stop"));
  Serial.println(F("  P <0-255>    speed used by F/B/L/R"));
  Serial.println(F("  I            show per-motor invert flags"));
  Serial.println(F("  I <n> <0|1>  flip motor n's forward direction (saved)"));
  Serial.println(F("  W            save config to flash"));
  Serial.println(F("  ? H          status / this help"));
}

void printStatus() {
  Serial.print(F("L=")); Serial.print(currentL);
  Serial.print('/');     Serial.print(targetL);
  Serial.print(F(" R=")); Serial.print(currentR);
  Serial.print('/');      Serial.print(targetR);
  Serial.print(F(" spd=")); Serial.print(cfg.speedVal);
  Serial.print(F(" pwmHz=")); Serial.print(PWM_FREQ_HZ);
  Serial.print(F(" wdt=")); Serial.print(wdtTripped ? "TRIPPED" : "ok");
  Serial.print(F(" inv="));
  for (int i = 0; i < 6; i++) Serial.print(cfg.invert[i]);
  Serial.println();
}

void handleLine(char *s) {
  while (*s == ' ') s++;
  if (*s == '\0') return;
  char cmd = toupper(*s);

  switch (cmd) {
    case 'V': {
      int l, r;
      if (sscanf(s + 1, "%d %d", &l, &r) == 2) {
        targetL = constrain(l, -255, 255);
        targetR = constrain(r, -255, 255);
        motorTestMs = 0;
        feedWatchdog();
      } else {
        Serial.println(F("ERR usage: V <left> <right>"));
      }
      break;
    }
    case 'M': {
      int n, pwm;
      if (sscanf(s + 1, "%d %d", &n, &pwm) == 2 && n >= 1 && n <= 6) {
        hardStop();
        pwm = constrain(pwm, -255, 255);
        driveMotor(MOTORS[n - 1], pwm);
        motorTestMs = millis();
        feedWatchdog();
        Serial.print(F("motor ")); Serial.print(n);
        Serial.print(F(" (")); Serial.print(MOTOR_NAME[n - 1]);
        Serial.print(F(") pwm=")); Serial.print(pwm);
        Serial.print(F("  auto-stop in ")); Serial.print(MOTOR_TEST_MS);
        Serial.println(F(" ms"));
      } else {
        Serial.println(F("ERR usage: M <1-6> <pwm>"));
      }
      break;
    }
    case 'G': {
      // Several chosen motors at once, for wiring checks. Same auto-stop as
      // M. mask bit 0 = motor 1 ... bit 5 = motor 6 (e.g. 5 = motors 1+3).
      int mask, pwm;
      if (sscanf(s + 1, "%d %d", &mask, &pwm) == 2 && mask >= 1 && mask <= 63) {
        hardStop();
        pwm = constrain(pwm, -255, 255);
        for (int i = 0; i < 6; i++)
          if (mask & (1 << i)) driveMotor(MOTORS[i], pwm);
        motorTestMs = millis();
        feedWatchdog();
        Serial.print(F("motors mask=")); Serial.print(mask);
        Serial.print(F(" pwm=")); Serial.print(pwm);
        Serial.print(F("  auto-stop in ")); Serial.print(MOTOR_TEST_MS);
        Serial.println(F(" ms"));
      } else {
        Serial.println(F("ERR usage: G <mask 1-63> <pwm>"));
      }
      break;
    }
    case 'F': targetL =  cfg.speedVal; targetR =  cfg.speedVal; motorTestMs = 0; feedWatchdog(); break;
    case 'B': targetL = -cfg.speedVal; targetR = -cfg.speedVal; motorTestMs = 0; feedWatchdog(); break;
    case 'L': targetL = -cfg.speedVal; targetR =  cfg.speedVal; motorTestMs = 0; feedWatchdog(); break;
    case 'R': targetL =  cfg.speedVal; targetR = -cfg.speedVal; motorTestMs = 0; feedWatchdog(); break;
    case 'S': hardStop(); feedWatchdog(); Serial.println(F("Stopped")); break;
    case 'P': {
      int p;
      if (sscanf(s + 1, "%d", &p) == 1) {
        cfg.speedVal = constrain(p, 0, 255);
        configSave();
        Serial.print(F("cfg.speedVal=")); Serial.println(cfg.speedVal);
        feedWatchdog();
      }
      break;
    }
    case 'I': {
      int n, v;
      int got = sscanf(s + 1, "%d %d", &n, &v);
      if (got == 2 && n >= 1 && n <= 6) {
        cfg.invert[n - 1] = v ? 1 : 0;
        hardStop();
        configSave();
        printInvert();
      } else if (got <= 0) {
        printInvert();
      } else {
        Serial.println(F("ERR usage: I <1-6> <0|1>   or   I"));
      }
      feedWatchdog();
      break;
    }
    case 'W': configSave(); break;
    case '?': printStatus(); break;
    case 'H': printHelp(); break;
    default:
      Serial.println(F("ERR use V <l> <r> | M <n> <pwm> | G <mask> <pwm> | F B L R S | P <n> | ? H"));
      break;
  }
}

// ───────────────────────── setup / loop ─────────────────────────
void setup() {
  configLoad();

  for (int i = 0; i < 6; i++) {
    pinMode(MOTORS[i].pwm, OUTPUT);
    pinMode(MOTORS[i].dir, OUTPUT);
  }

  // 20 kHz, 8-bit. Must be set before the first analogWrite to take effect.
  analogWriteFreq(PWM_FREQ_HZ);
  analogWriteRange(255);

  hardStop();

  Serial.begin(115200);
  Serial.println();
  printHelp();
  printInvert();
  lastCmdMs = millis();
}

void loop() {
  // -- accumulate a line, act on newline --
  while (Serial.available() > 0) {
    char c = Serial.read();
    if (c == '\n' || c == '\r') {
      if (lineLen > 0) {
        lineBuf[lineLen] = '\0';
        handleLine(lineBuf);
        lineLen = 0;
      }
    } else if (lineLen < sizeof(lineBuf) - 1) {
      lineBuf[lineLen++] = c;
    } else {
      lineLen = 0;             // overflow: drop the garbage line
    }
  }

  unsigned long now = millis();

  // -- single-motor test auto-stop --
  if (motorTestMs && (now - motorTestMs) > MOTOR_TEST_MS) {
    hardStop();
    Serial.println(F("motor test ended"));
  }

  // -- watchdog: host went quiet --
  // A running "M" test is exempt: it is a deliberate one-shot with its own
  // shorter-intent timeout, and the operator is not streaming commands
  // during it.  Without this the 500 ms watchdog would cut every wiring
  // check short at 500 ms instead of MOTOR_TEST_MS.
  if (!wdtTripped && !motorTestMs && (now - lastCmdMs) > WATCHDOG_MS) {
    wdtTripped = true;
    hardStop();
    Serial.println(F("WDT stop (no command)"));
  }

  // -- slew-limited ramp toward target --
  if (!wdtTripped && !motorTestMs && (now - lastRampMs) >= RAMP_INTERVAL_MS) {
    lastRampMs = now;
    int newL = stepToward(currentL, targetL);
    int newR = stepToward(currentR, targetR);
    if (newL != currentL || newR != currentR) {
      currentL = newL;
      currentR = newR;
      applyMotors();
    }
  }
}

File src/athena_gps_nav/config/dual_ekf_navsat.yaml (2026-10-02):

# ============================================================================
# Dual-EKF + navsat_transform configuration for the Athena rover
# (robot_localization 3.5.x, ROS 2 Humble)
#
# Sensor inputs:
#   /vio/odometry  rtabmap rgbd_odometry (D435i)   -> fuse BODY VELOCITIES
#   /imu/data      Pixhawk (ENU-converted, has absolute compass yaw)
#   /odometry/gps  navsat_transform output          -> fuse absolute x/y (map EKF)
#
# Design notes (from robot_localization docs + Nav2 GPS tutorial):
#  * VIO is fused as velocities (vx, vy, vyaw), never as pose: VO drift then
#    integrates in the filter instead of fighting the GPS, and VO auto-resets
#    (Odom/ResetCountdown) cause no pose jumps.
#  * The Pixhawk yaw is the ONLY absolute heading source (D435i has no mag).
#    If compass yaw proves unreliable near the motors, set
#    imu0_differential: true in BOTH filters and set
#    navsat_transform use_odometry_yaw: false -> heading then converges from
#    GPS + motion (needs some driving before it is correct).
#  * two_d_mode everywhere: this is a ground rover.
# ============================================================================

ekf_local:
  ros__parameters:
    frequency: 30.0
    sensor_timeout: 0.2
    two_d_mode: true
    transform_time_offset: 0.0
    transform_timeout: 0.0
    print_diagnostics: true
    publish_tf: true            # owns odom -> base_link

    map_frame: map
    odom_frame: odom
    base_link_frame: base_link
    world_frame: odom

    # --- VIO: velocities only ---
    odom0: /vio/odometry
    odom0_config: [false, false, false,     # x y z
                   false, false, false,     # roll pitch yaw
                   true,  true,  false,     # vx vy vz
                   false, false, true,      # vroll vpitch vyaw
                   false, false, false]     # ax ay az
    odom0_queue_size: 10
    odom0_nodelay: true
    odom0_differential: false
    odom0_relative: false
    # NOTE: no odom0_twist_rejection_threshold here.  A Mahalanobis gate
    # self-locks: one accepted spike drives the state away, then all the
    # honest measurements look like outliers and get rejected forever
    # (observed on the bench: 1.7 m/s phantom runaway).  Physical outlier
    # rejection lives in the vio_gate node instead.

    # --- Pixhawk IMU: yaw RATE only in the local filter ---
    # Absolute compass yaw is fused only in the global EKF: at 48 Hz the
    # absolute-yaw corrections cross-couple into the velocity states and
    # measurably pump position jitter (bench: EKF vx noise 2-3x the VIO
    # measurement noise until this was removed).  The odom frame is
    # allowed to have slowly drifting yaw per REP-105.
    imu0: /imu/data
    imu0_config: [false, false, false,
                  false, false, false,
                  false, false, false,
                  false, false, true,       # vyaw
                  false, false, false]      # accels off: vibration noise
    imu0_queue_size: 20
    imu0_nodelay: true
    imu0_differential: false
    imu0_relative: false
    imu0_remove_gravitational_acceleration: true

    use_control: false
    # Scale process noise with velocity: keeps the estimate pinned when the
    # rover is stationary (kills stationary drift).
    dynamic_process_noise_covariance: true

    # Q diagonal (x y z r p y | vx vy vz vr vp vy | ax ay az)
    process_noise_covariance: [1.0e-3, 0.0, 0.0, 0.0, 0.0, 0.0, 0.0, 0.0, 0.0, 0.0, 0.0, 0.0, 0.0, 0.0, 0.0,
                               0.0, 1.0e-3, 0.0, 0.0, 0.0, 0.0, 0.0, 0.0, 0.0, 0.0, 0.0, 0.0, 0.0, 0.0, 0.0,
                               0.0, 0.0, 1.0e-3, 0.0, 0.0, 0.0, 0.0, 0.0, 0.0, 0.0, 0.0, 0.0, 0.0, 0.0, 0.0,
                               0.0, 0.0, 0.0, 0.3, 0.0, 0.0, 0.0, 0.0, 0.0, 0.0, 0.0, 0.0, 0.0, 0.0, 0.0,
                               0.0, 0.0, 0.0, 0.0, 0.3, 0.0, 0.0, 0.0, 0.0, 0.0, 0.0, 0.0, 0.0, 0.0, 0.0,
                               0.0, 0.0, 0.0, 0.0, 0.0, 0.01, 0.0, 0.0, 0.0, 0.0, 0.0, 0.0, 0.0, 0.0, 0.0,
                               0.0, 0.0, 0.0, 0.0, 0.0, 0.0, 0.001, 0.0, 0.0, 0.0, 0.0, 0.0, 0.0, 0.0, 0.0,
                               0.0, 0.0, 0.0, 0.0, 0.0, 0.0, 0.0, 0.001, 0.0, 0.0, 0.0, 0.0, 0.0, 0.0, 0.0,
                               0.0, 0.0, 0.0, 0.0, 0.0, 0.0, 0.0, 0.0, 0.1, 0.0, 0.0, 0.0, 0.0, 0.0, 0.0,
                               0.0, 0.0, 0.0, 0.0, 0.0, 0.0, 0.0, 0.0, 0.0, 0.3, 0.0, 0.0, 0.0, 0.0, 0.0,
                               0.0, 0.0, 0.0, 0.0, 0.0, 0.0, 0.0, 0.0, 0.0, 0.0, 0.3, 0.0, 0.0, 0.0, 0.0,
                               0.0, 0.0, 0.0, 0.0, 0.0, 0.0, 0.0, 0.0, 0.0, 0.0, 0.0, 0.002, 0.0, 0.0, 0.0,
                               0.0, 0.0, 0.0, 0.0, 0.0, 0.0, 0.0, 0.0, 0.0, 0.0, 0.0, 0.0, 0.3, 0.0, 0.0,
                               0.0, 0.0, 0.0, 0.0, 0.0, 0.0, 0.0, 0.0, 0.0, 0.0, 0.0, 0.0, 0.0, 0.3, 0.0,
                               0.0, 0.0, 0.0, 0.0, 0.0, 0.0, 0.0, 0.0, 0.0, 0.0, 0.0, 0.0, 0.0, 0.0, 0.3]
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

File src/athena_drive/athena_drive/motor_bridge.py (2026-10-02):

#!/usr/bin/env python3
"""
motor_bridge.py. /cmd_vel to the Pico motor controller.

Converts geometry_msgs/Twist into signed per-side PWM and streams it to the
Pico running athena_drive_fw:

    V <left> <right>\\n     -255..255 per side, positive = forward

Design notes
------------
Skid-steer kinematics:  v_left = v - w*W/2,  v_right = v + w*W/2

* **Curvature-preserving saturation.**  If either side exceeds the maximum
  wheel speed, BOTH sides scale down by the same factor.  Clipping them
  independently would change the ratio between them, which is what sets the
  turn radius - the rover would silently drive a different arc than Nav2
  asked for, and worse at exactly the moments it is trying hardest to turn.

* **Deadband compensation.**  A DC motor does not move at all below some
  duty cycle.  Any non-zero wheel speed is mapped into [min_pwm, 255] so
  small corrections actually reach the ground instead of being swallowed by
  static friction.

* **Streaming, not event-driven.**  Commands go out at send_rate regardless
  of when /cmd_vel arrives, so the firmware watchdog sees a steady heartbeat
  and only trips on a genuine failure.

* **Two independent watchdogs.**  This node zeroes the target if /cmd_vel
  goes stale; the firmware stops the motors if the serial link goes quiet.
  Either alone leaves a gap - a live node sending stale commands, or a dead
  cable with the motors latched on.

Ports are auto-detected by USB id.  Never hard-code /dev/ttyACM<n>: those
numbers are assigned in enumeration order and swap between boots.  On this
rover the Pixhawk and the Pico have each held ttyACM0 on different days, and
sending motor commands to a flight controller is the failure this prevents.
"""

import glob
import os
import threading
import time

import rclpy
from rclpy.node import Node
from geometry_msgs.msg import Twist
from std_msgs.msg import String

from athena_drive.velocity_profile import VelocityProfile

PICO_GLOB = '/dev/serial/by-id/usb-Raspberry_Pi_Pico*'

# Written by `ros2 run athena_drive calibrate` and read here at startup, so
# calibrated values apply to every launch without command-line arguments.
# Kept outside the package so a rebuild or reinstall cannot wipe it.
#
# Motor DIRECTIONS are deliberately NOT here: they live in the Pico's own
# flash. Direction is a property of the wiring, so it belongs to the board -
# swap in a different Jetson and the motors still spin the right way.
CONFIG_PATH = os.path.expanduser('~/.config/athena_drive/params.yaml')

# Values the calibration wizard writes. Side inversion is NOT among them -
# that is per-motor and lives in the Pico's flash.
_CALIBRATED = ('track_width', 'max_wheel_speed', 'min_pwm', 'max_pwm')


def load_calibration(logger=None):
    """Return saved calibration as a dict, or {} if there is none."""
    if not os.path.exists(CONFIG_PATH):
        if logger:
            logger.warn(
                f'No calibration at {CONFIG_PATH} - using built-in estimates. '
                'Run:  ros2 run athena_drive calibrate')
        return {}
    try:
        import yaml
        with open(CONFIG_PATH) as f:
            data = yaml.safe_load(f) or {}
        out = {k: v for k, v in data.items() if k in _CALIBRATED}
        if logger:
            logger.info(f'loaded calibration from {CONFIG_PATH}: {out}')
        return out
    except Exception as e:
        if logger:
            logger.error(f'could not read {CONFIG_PATH}: {e}')
        return {}


def find_pico(logger=None):
    """Stable by-id path of the Pico, or None with a logged reason.

    Globs rather than pinning one serial: the by-id name embeds the flash
    serial, which changes if the board itself is swapped.
    """
    hits = sorted(glob.glob(PICO_GLOB))
    if not hits:
        if logger:
            logger.error(f'No Pico found matching {PICO_GLOB} - is it plugged in?')
        return None
    if len(hits) > 1 and logger:
        logger.warn(f'{len(hits)} Picos present, using {hits[0]}: {hits}')
    return hits[0]


class MotorBridge(Node):
    def __init__(self):
        super().__init__('motor_bridge')

        self.declare_parameter('port', '')               # '' = auto-detect
        self.declare_parameter('baud', 115200)
        self.declare_parameter('send_rate', 20.0)        # Hz
        # -1 means "not given" -> fall back to the saved calibration, then
        # to the built-in estimate. An explicit value always wins, so a
        # one-off experiment never silently becomes permanent.
        self.declare_parameter('track_width', -1.0)      # m between wheel centres
        self.declare_parameter('max_wheel_speed', -1.0)  # m/s at PWM 255
        self.declare_parameter('min_pwm', -1)            # static-friction deadband
        self.declare_parameter('max_pwm', -1)            # cap for cautious testing
        self.declare_parameter('watchdog_timeout', 0.5)  # s of stale cmd_vel
        # Velocity profile. Limiting acceleration alone still lets the
        # acceleration itself change instantly - that step is the lurch you
        # feel starting and the nod you see stopping, and it shakes the very
        # camera the visual odometry depends on. Bounding jerk too gives an
        # S-curve: the pull eases in, holds, then eases out.
        self.declare_parameter('profile_enabled', True)
        self.declare_parameter('max_accel', 0.5)       # m/s^2
        self.declare_parameter('max_jerk', 1.0)        # m/s^3
        self.declare_parameter('max_ang_accel', 1.5)   # rad/s^2
        self.declare_parameter('max_ang_jerk', 3.0)    # rad/s^3
        self.declare_parameter('invert_left', False)
        self.declare_parameter('invert_right', False)
        self.declare_parameter('dry_run', False)

        # precedence: explicit argument > saved calibration > estimate
        cal = load_calibration(self.get_logger())
        FALLBACK = {'track_width': 0.40, 'max_wheel_speed': 0.7,
                    'min_pwm': 40, 'max_pwm': 255}

        # Which values ended up as guesses.  Tracked per key, not per file:
        # a calibration that exists but is INCOMPLETE used to count as fully
        # calibrated, so the rover would silently run on the 0.7 m/s estimate
        # with no warning anywhere.  That is the live state of this rover -
        # the saved file has min_pwm and track_width but not max_wheel_speed
        # or max_pwm - and max_wheel_speed scales every velocity Nav2 asks
        # for, so it is exactly the value you least want quietly guessed.
        self._estimated = []

        def pick(name, cast):
            given = self.get_parameter(name).value
            if given is not None and cast(given) >= 0:
                return cast(given)                  # explicitly passed
            if name in cal:
                return cast(cal[name])              # from calibration
            self._estimated.append(name)
            return cast(FALLBACK[name])             # built-in estimate
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

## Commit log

2026-06-06 Simple Rocker Bogie sim
    [mount.blend1.obj, rover.urdf, terrain1.obj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]
2026-06-06 minor changes
    [rover.urdf]
2026-06-06 Add files via upload
    added camera
    [rover.urdf]
2026-06-06 "Ros2 workspace files"
    [base_link.stl, bogie_left_1.stl, bogie_right_1.stl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]
